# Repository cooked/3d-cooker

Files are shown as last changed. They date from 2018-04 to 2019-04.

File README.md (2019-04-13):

# wreck3D 

The wreck3D is a parametric delta printer built around the OpenBuilds V-Slot 2040 linear rails.   

The wreck3D design is made simple so that the built is achieved, with the same minimal set of 3D printed parts, in virtually any form-factor the OpenBuilds rails allow.

## Size
List of the build sizes readily available:  

* wreck3D-S (Build Volume: 200x185 mm) 
* wreck3D-M (Build Volume: 250x300 mm)

[3D printed parts](printed-parts) - [Bill of Material](bom/bom.csv) - [Manual](https://github.com/wreck-lab/wreck3D/wiki)
   
##
      
Analytics (https://github.com/igrigorik/ga-beacon)

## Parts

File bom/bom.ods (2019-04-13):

Item | Quantity | Note | Source
OpenBuild VSlot 2040 1000mm | 3 | Frame S – cut to 250 + 250 + 500 mm | RatRig (http://www.ratrig.com/hardware2/vslot/v-slot-2040.html))
OpenBuild VSlot 2040 1000mm | 3 | Frame M - cut to 300 + 700 mm | RatRig (http://www.ratrig.com/hardware2/vslot/v-slot-2040.html))
OpenBuild VSlot 2020 1000mm | 2 | Frame M - cut to 300 + 300 +300 mm | RatRig (http://www.ratrig.com/hardware2/vslot/v-slot-2020.html))
carbon fiber tube 8x6x500mm | 3 | Frame S – request cuts of 245 mm each The length of the arms doesn't need to be the exact but SHALL BE THE SAME for all of them. Trim them down with sandpaper if the difference is visible to the naked eye | AliExpress (https://www.aliexpress.com/item/2pcs-3K-Matte-Twill-Carbon-Fiber-Tube-Pipe-OD-8mm-ID-6mm-Length-500mm-Tubes-Twill/32760008446.html)
carbon fiber tube 8x6x1000mm | 2 | Frame M – request cuts of 330 mm each The length of the arms doesn't need to be the exact but SHALL BE THE SAME for all of them. Trim them down with sandpaper if the difference is visible to the naked eye | AliExpress (https://www.aliexpress.com/item/2pcs-3K-Matte-Twill-Carbon-Fiber-Tube-Pipe-OD-8mm-ID-6mm-Length-500mm-Tubes-Twill/32760008446.html)
220x3mm round aluminum heat bed | 1 |  | AliExpress (https://www.aliexpress.com/item/MK3-Heat-bed-220-3mm-Aluminum-Heatbed-dual-power-12V-or-24V-round-PCB-Heat-bed/32810724832.html)
OpenBuild VSlot mini wheel | 9 | 3x each carriage | AliExpress (https://www.aliexpress.com/item/10pcs-Openbuilds-V-Slot-Linear-Extrusion-Wheels-Delrin-plastic-Idler-Pulley-For-guide-rail-3D-Printer/32623054810.html)
NEMA 17 stepper motor | 4 | cable included | AliExpress (https://www.aliexpress.com/item/5pcs-lot-Free-Shipping-3D-printer-4-lead-Nema17-Stepper-Motor-42-motor-Nema-17-motor/32728425552.html)
GT2 Pulley 20 teeth 5mm bore | 3 | lock on motor shaft with set screws | AliExpress (https://www.aliexpress.com/item/POWGE-GT2-Timing-Pulley-20-teeth-Bore-5mm-6mm-6-35mm-8mm-for-Width-6mm-GT2/32226562320.html)
GT2 Pulley 16 teeth 3mm bore | 3 |  | AliExpress (https://www.aliexpress.com/item/New-GT2-Idler-Timing-Pulley-Bearing-20T-3-5mm-Bore-20-Teeth-Suitable-For-6mm-Belt/32823859861.html)
GT2 Timing Belt 6mm width | 6m |  | AliExpress (https://www.aliexpress.com/item/POWGE-GT2-timing-belt-width-6mm-Rubber-2GT-6mm-used-in-linear-drive-Small-Backlash-2GT/2039635559.html)
10mm steel ball M4 thread | 12 | 3x carriages 3x effector | AliExpress (https://www.aliexpress.com/item/High-Quality-Brand-New-16pcs-Set-10mm-M4-Threaded-Steel-Ball-Rod-Ends-For-Kossel-3D/32646492682.html)
6x13mm magnet rod | 12 | 2x each arm | Supermagnete (https://www.supermagnete.de/eng/rod-magnets-neodymium/rod-magnet-diameter-6mm-height-13mm-neodymium-n48-nickel-plated_S-06-13-N)
V6 lite hotend kit |  | or original V6 all-metal hotend | e3d-online (https://e3d-online.com/lite6)
12V 15A power supply | 1 |  | AliExpress (https://www.aliexpress.com/item/2016-Brand-New-Mini-Size-Led-Power-Supply-12V-5A-8-5A-10A-12-5A-15A/32571488140.html)
KW-1-2A micro switch | 1 | remove lever | AliExpress (https://www.aliexpress.com/item/Free-Shipping-100pcs-KW-1-2A-Small-lever-micro-limit-switch/32546855308.html)
KW11-B switch | 3 | remove lever | AliExpress (https://www.aliexpress.com/item/50-pieces-lot-KW11-B-microswitch-3pins-3P-5A-125-250V-10T85-18mm-long-handle/32528115223.html)
40x10mm radial blow fan | 2 | 2x effector print cooling fan | AliExpress (https://www.aliexpress.com/item/2PCS-Gdstime-3D-Printer-Accessories-12V-4010-Turbo-Fan-Blower-Cooling-Fans/32798634077.html)
M5x8mm hex screw low profile | 100 | 12x each motor and idler corner | AliExpress (https://www.aliexpress.com/item/Low-profile-screws-M5-8-100pcs/32660374302.html)
M5 T-nut hammer head | 100 | 12x each motor and idler corner | AliExpress (https://www.aliexpress.com/item/100pcs-lot-High-Quality-T-nut-Hammer-Head-Fasten-Nut-M5-Connector-Nickel-Plated-for-20/32716318190.html)
M4x10mm screw DIN 912 | 12 | 3x carriage 3x effector | AliExpress (https://www.aliexpress.com/item/M4-series-100pcs-Stainless-steel-hex-socket-screws-M4-4-5-6-8-10-12-30/32662311536.html)
M5x20mm screw DIN 912 | 3 | idler pulley mount | AliExpress (https://www.aliexpress.com/item/QINTIDES-M5-Hexagon-socket-head-cap-screws-304-stainless-steel-hexagon-screw-DIN-912-M5/32860098615.html)
M5x16mm screw DIN 912 | 9 | 3x carriage wheels | AliExpress (https://www.aliexpress.com/item/QINTIDES-M5-Hexagon-socket-head-cap-screws-304-stainless-steel-hexagon-screw-DIN-912-M5/32860098615.html)
M3x10mm screw DIN 912 | 12 | 4x each stepper motor mount | AliExpress (https://www.aliexpress.com/item/250pc-set-M3-Cap-Button-Flat-Head-A2-Stainless-Steel-Hex-Socket-Screws-Bolt-With-Hex/32775208136.html)
M3x20mm screw DIN 912 | 1 | 1x effector tower spring | AliExpress (https://www.aliexpress.com/item/250pc-set-M3-Cap-Button-Flat-Head-A2-Stainless-Steel-Hex-Socket-Screws-Bolt-With-Hex/32775208136.html)
M3x30mm screw DIN 912 | 2 | 2x effector tower collar | AliExpress (https://www.aliexpress.com/item/250pc-set-M3-Cap-Button-Flat-Head-A2-Stainless-Steel-Hex-Socket-Screws-Bolt-With-Hex/32775208136.html)
M3x40mm screw DIN 912 | 1 | 1x effector tower rotation | AliExpress (https://www.aliexpress.com/item/250pc-set-M3-Cap-Button-Flat-Head-A2-Stainless-Steel-Hex-Socket-Screws-Bolt-With-Hex/32775208136.html)
M2.5x12mm screw DIN 912 | 6 | 6x endstop switches | AliExpress (https://www.aliexpress.com/item/100pcs-Lot-Metric-Thread-DIN912-M2-5x12-mm-M2-5-12-mm-Black-Grade-12-9/32808680386.html)
M3 nut | 9 | 3x for effector 3x belt lock mounts 3x belt tensioners | AliExpress (https://www.aliexpress.com/item/Free-shipping-100pcs-lot-Metric-thread-DIN934-M3-304-Stainless-Steel-Hex-Nuts/32405600179.html)
M2x8mm screw self tapping | 4 | 2x (each) effector print cooling fan | AliExpress (https://www.aliexpress.com/item/100pcs-Lot-Metric-Thread-carbon-steel-Hex-Socket-Head-Cap-self-tapping-Screw-Bolts-M2x8/32497369062.html)
3mm grommet | 1 | 1x effector tower spring | AliExpress (https://www.aliexpress.com/item/130pcs-3mm-Inner-Dia-Double-Sides-Wire-Grommets-Gasket-Cable-Protector/32824763799.html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)

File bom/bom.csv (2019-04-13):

Item | Quantity | Note | Source
OpenBuild VSlot 2040 1000mm | 3 | Frame S - cut to 250 + 250 + 500 mm | RatRig
OpenBuild VSlot 2040 1000mm | 3 | Frame M - cut to 300 + 700 mm | RatRig
OpenBuild VSlot 2020 1000mm | 2 | Frame M - cut to 300 + 300 +300 mm | RatRig
carbon fiber tube 8x6x500mm | 3 | Frame S – request cuts of 245 mm each The length of the arms doesn't need to be the exact but SHALL BE THE SAME for all of them. Trim them down with sandpaper if the difference is visible to the naked eye | AliExpress
carbon fiber tube 8x6x1000mm | 2 | Frame M – request cuts of 330 mm each The length of the arms doesn't need to be the exact but SHALL BE THE SAME for all of them. Trim them down with sandpaper if the difference is visible to the naked eye | AliExpress
220x3mm round aluminum heat bed | 1 |  | AliExpress
OpenBuild VSlot mini wheel | 9 | 3x each carriage | AliExpress
NEMA 17 stepper motor | 4 | cable included | AliExpress
GT2 Pulley 20 teeth 5mm bore | 3 | lock on motor shaft with set screws | AliExpress
GT2 Pulley 16 teeth 3mm bore | 3 |  | AliExpress
GT2 Timing Belt 6mm width | 6m |  | AliExpress
10mm steel ball M4 thread | 12 | 3x carriages 3x effector | AliExpress
6x13mm magnet rod | 12 | 2x each arm | Supermagnete
V6 lite hotend kit |  | or original V6 all-metal hotend | e3d-online
12V 15A power supply | 1 |  | AliExpress
KW-1-2A micro switch | 1 | remove lever | AliExpress
KW11-B switch | 3 | remove lever | AliExpress
40x10mm radial blow fan | 2 | 2x effector print cooling fan | AliExpress
M5x8mm hex screw low profile | 100 | 12x each motor and idler corner | AliExpress
M5 T-nut hammer head | 100 | 12x each motor and idler corner | AliExpress
M4x10mm screw DIN 912 | 12 | 3x carriage 3x effector | AliExpress
M5x20mm screw DIN 912 | 3 | idler pulley mount | AliExpress
M5x16mm screw DIN 912 | 9 | 3x carriage wheels | AliExpress
M3x10mm screw DIN 912 | 12 | 4x each stepper motor mount | AliExpress
M3x20mm screw DIN 912 | 1 | 1x effector tower spring | AliExpress
M3x30mm screw DIN 912 | 2 | 2x effector tower collar | AliExpress
M3x40mm screw DIN 912 | 1 | 1x effector tower rotation | AliExpress
M2.5x12mm screw DIN 912 | 6 | 6x endstop switches | AliExpress
M3 nut | 9 | 3x for effector 3x belt lock mounts 3x belt tensioners | AliExpress
M2x8mm screw self tapping | 4 | 2x (each) effector print cooling fan | AliExpress
3mm grommet | 1 | 1x effector tower spring | AliExpress

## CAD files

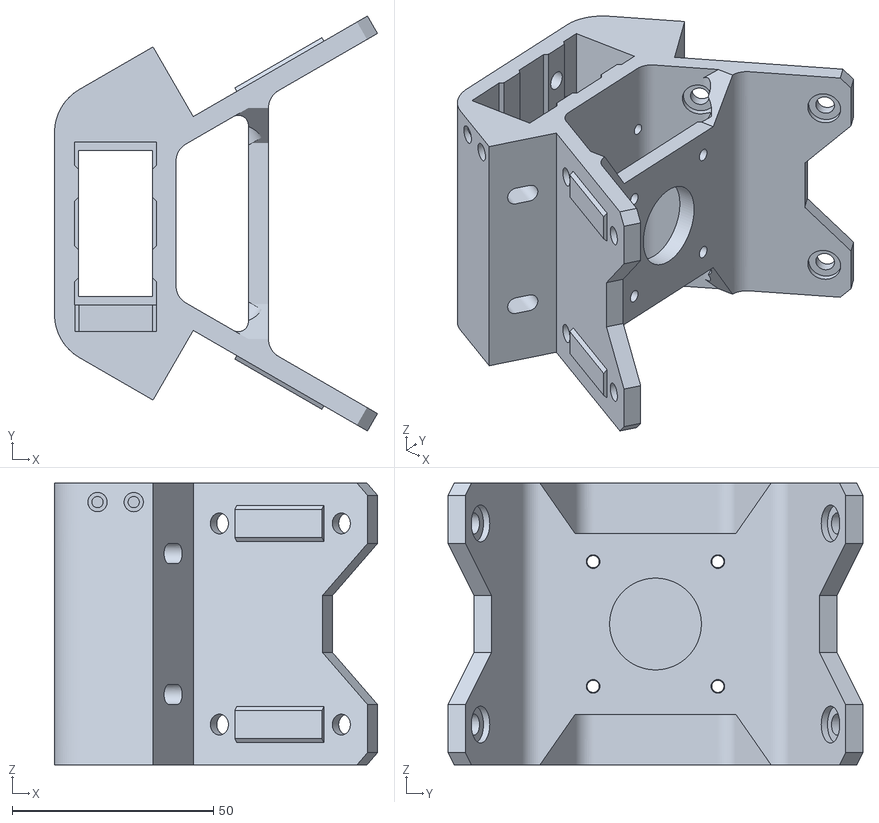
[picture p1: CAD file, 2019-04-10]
printed-parts/corner_motor_2.stl
80.3 x 103.2 x 70.0

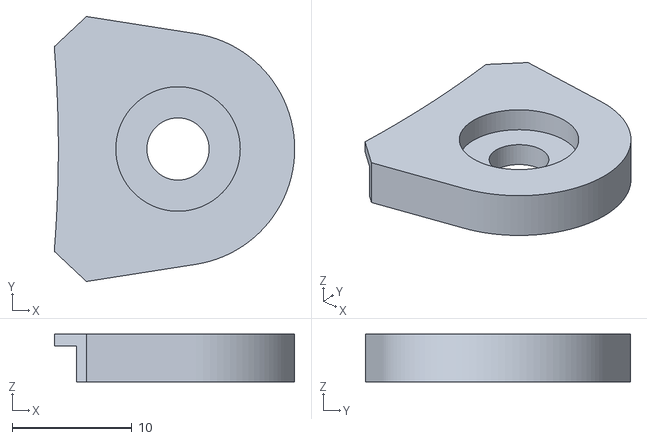
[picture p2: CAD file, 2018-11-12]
printed-parts/misc/bed_clamp_220x3mm.stl
20.1 x 22.1 x 4.00

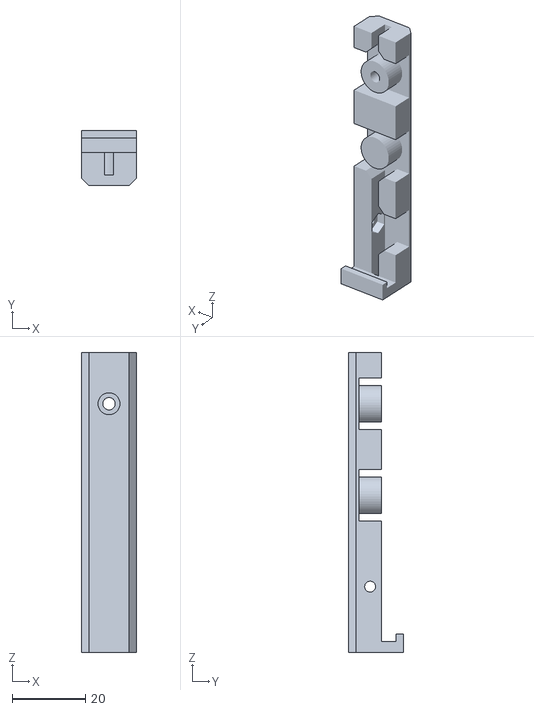
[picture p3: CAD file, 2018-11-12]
printed-parts/carriage_lock.stl
15.0 x 15.0 x 82.0

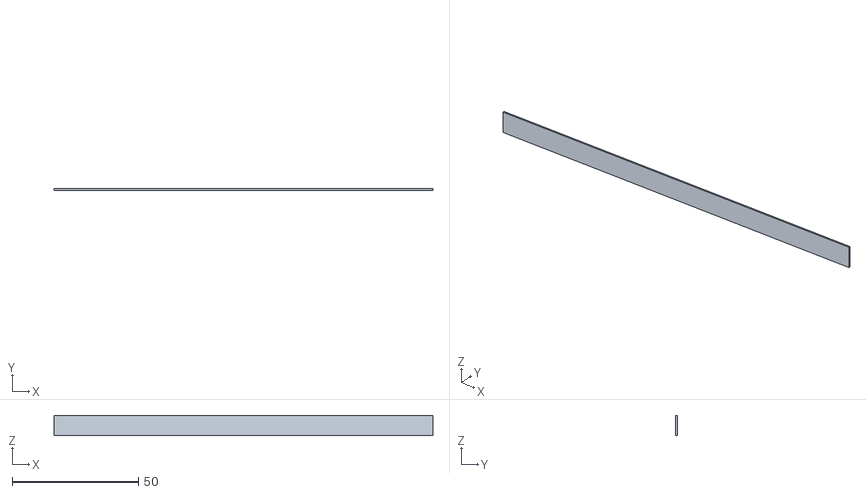
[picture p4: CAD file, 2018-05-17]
printed-parts/misc/rail_cover.stl
150.0 x 0.6 x 8.00

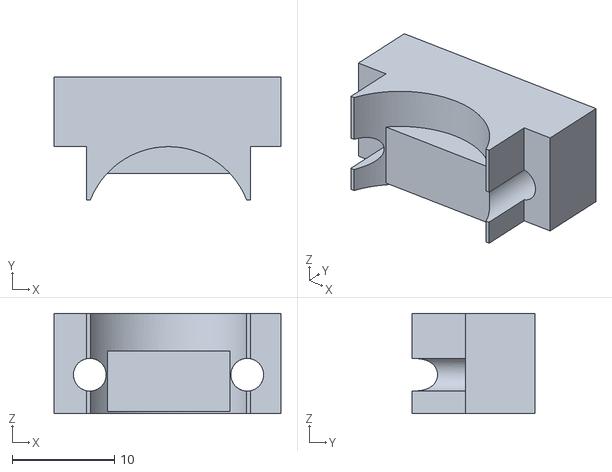
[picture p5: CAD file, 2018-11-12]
printed-parts/effector_collar.stl
22.2 x 12.0 x 9.80

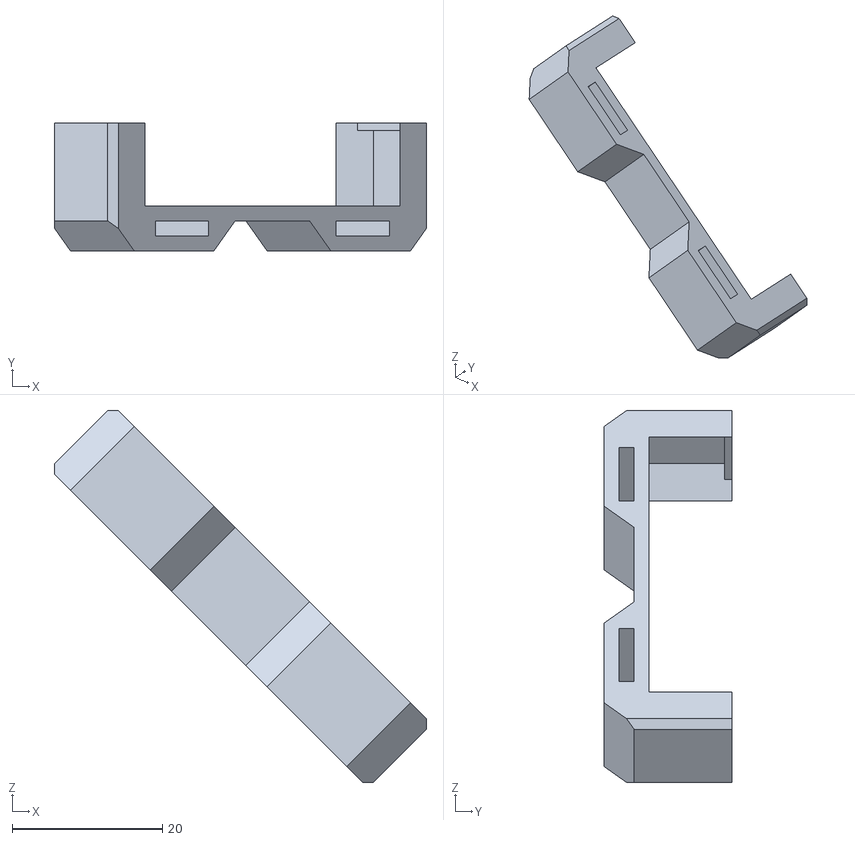
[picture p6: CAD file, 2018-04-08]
printed-parts/misc/motor_cable_organizer.stl
49.5 x 17.0 x 49.5

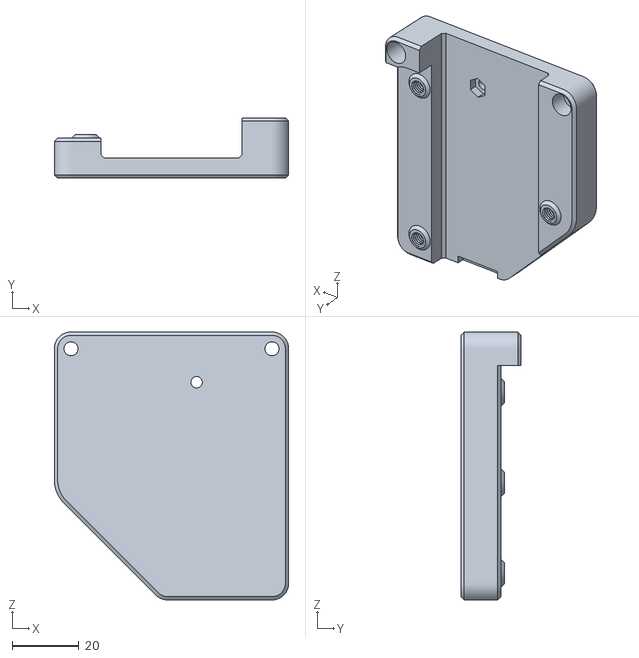
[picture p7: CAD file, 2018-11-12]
printed-parts/carriage_body.stl
70.0 x 18.0 x 80.0

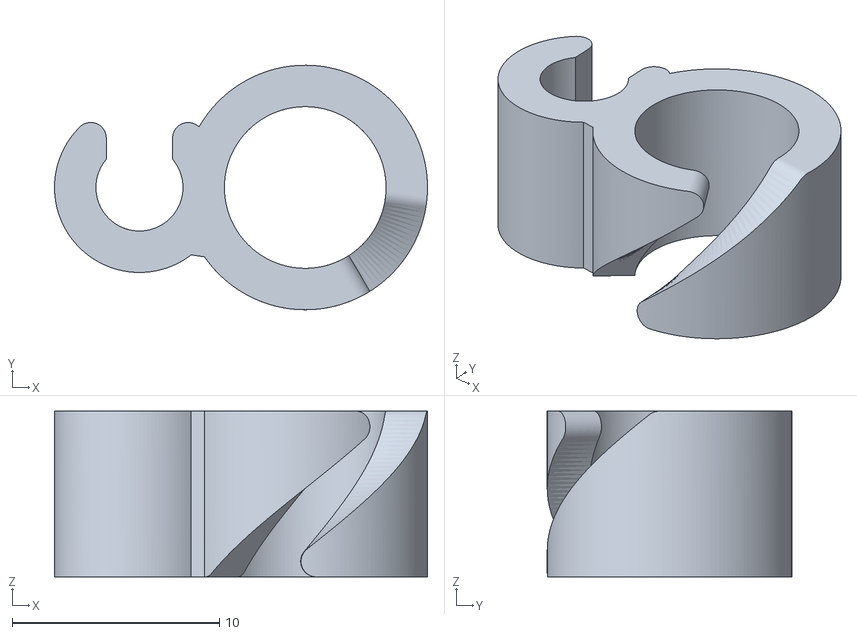
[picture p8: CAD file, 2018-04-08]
printed-parts/misc/cable_clip.stl
18.0 x 11.8 x 8.00

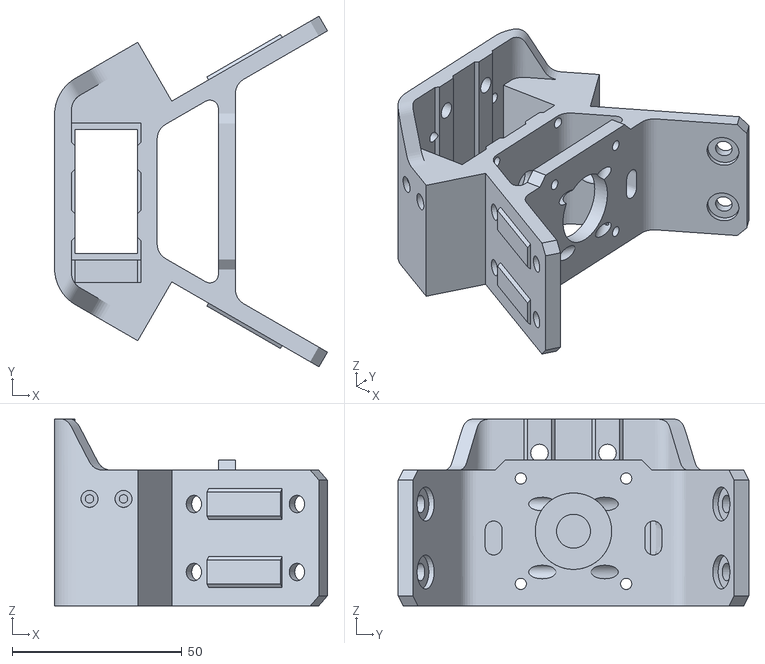
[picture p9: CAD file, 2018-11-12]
printed-parts/corner_motor.stl
80.3 x 103.2 x 55.0

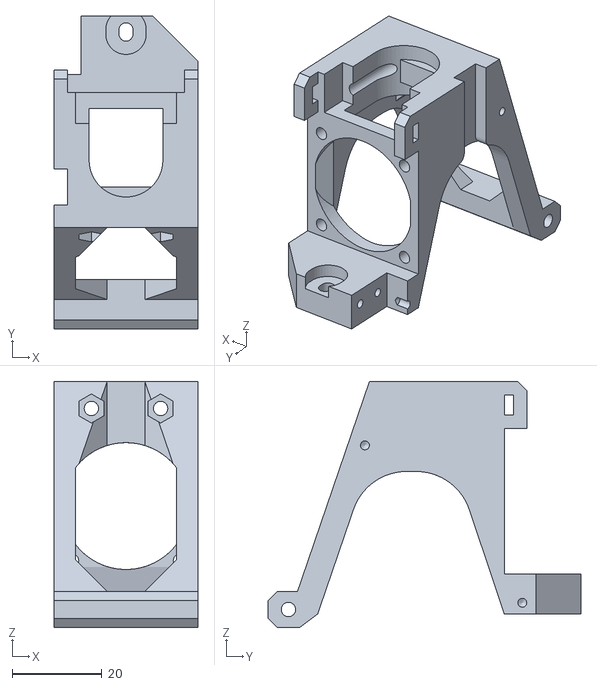
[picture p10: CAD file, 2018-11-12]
printed-parts/effector_tower.stl
32.0 x 69.5 x 54.7

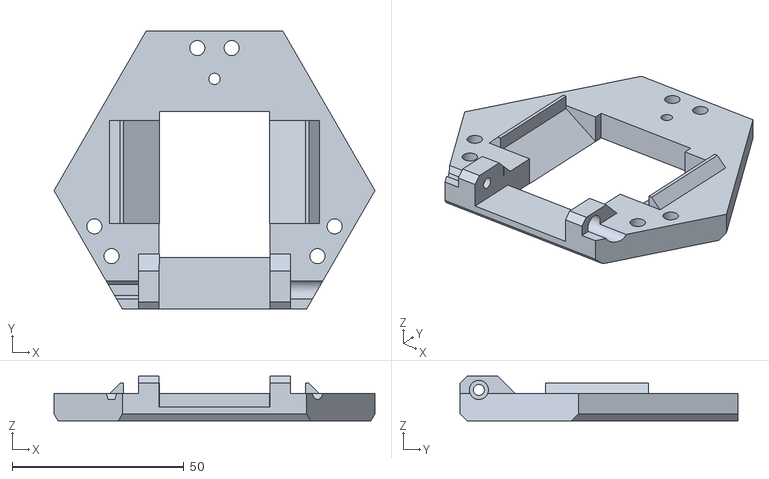
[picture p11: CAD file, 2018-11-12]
printed-parts/effector_base.stl
93.5 x 81.0 x 13.0

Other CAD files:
printed-parts/corner_idler.stl

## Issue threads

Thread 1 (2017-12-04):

M4 holes in the carriage are too small.

orlandod543, 2017-12-04:
The M4 screws to hold the steel balls have a round head with a diameter of 6.78mm. The hole in the carriage where they fit,  however is 6.58mm. Enhancing it to 7mm should fix the problem.

cooked, 2018-05-10:
- carriage updated to the new version (with the cut corner)
- M4 screw holes diameter is now 7.2 mm

Closed 2018-05-10.

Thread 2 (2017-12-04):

M3 screws and nuts are missing.

orlandod543, 2017-12-04:

cooked, 2018-05-10:
- added set of M3 screws to the BOM

Closed 2018-05-10.

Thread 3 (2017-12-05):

M5 screws for the bearings are missing.

orlandod543, 2017-12-05:
They should be 9 screws of 16mm long.

cooked, 2018-05-10:
- added M5x16 screws to the BOM

Closed 2018-05-10.

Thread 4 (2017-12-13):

Use 10mm m3 screws for the stepper motor

orlandod543, 2017-12-13:
10mm m3 screws are perfect to hold the stepper motors. Longer than that won't work

cooked, 2018-05-10:
- added set of M3 screws to the BOM
- added assembly instruction in the wiki

Closed 2018-05-10.

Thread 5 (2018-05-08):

Replace M5 nut of the idler mount with printed thread

cooked, 2018-05-08:

cooked, 2018-05-13:
updated STL

Closed 2018-05-13.

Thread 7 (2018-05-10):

Merge the BOMs

cooked, 2018-05-10:
- merge the BOM of the different printer sizes to make it easier to maintain
- use the column "notes" to add details on how parts are customized for the specific size

cooked, 2018-05-13:
single BOM created

Closed 2018-05-13.

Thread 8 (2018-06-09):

spheres distance in the effector plate is wrong

cooked, 2018-06-09:
adjacent sphere centers should be 60mm on the long side and 10mm on the short side.
on the long side the distance is currently 59.952

cooked, 2018-11-12:
the sphere holes have been moved to the correct distance of  60mm
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

Closed 2018-11-12.

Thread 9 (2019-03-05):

Print Area

sennalb, 2019-03-05:
Hi,
where I can find print area dimensions ?
Thanks

smark-, 2019-03-06:
> Hi,
> where I can find print area dimensions ?
> Thanks

The wreck3D-S has a build volume of 200x185 mm. I will add them to the Wiki

sennalb, 2019-03-07:
Since wrek3d-s is a parametric printer  is It possible to establish a printing area and obtain the respective dimensions of the towers, sides and rods.
 I have not yet found a calculation system at this level.
Obviously within certain limits, for example if I wanted to get a 250x300 printing area which could be the lengths of the towers, sides and rods?

smark-, 2019-03-08:
Given your volume requirements I would start from the wreck3D-M which has a build volume of 260x275. If you just increase the column height by 25 mm you can easily reach a total height of 300mm. We are planning to release the design files and the mounting instructions in mid April, as we did we the wreck3D-S. If you are need it sooner please send us an e-mail at info@wrecklab.com

Closed 2019-04-15.

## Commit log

2018-04-08 add STL
    [cable_clip.stl, carriage_belt_lock.stl, carriage_body.stl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]
2018-04-08 add settings Cura
    [3DC+mk3.global.cfg]
2018-04-08 add settings Marlin firmware
    [Configuration.h, Configuration_adv.h]
2018-05-08 added animation idler assembly
2018-05-10 updated effector to mk3
    [effector_base.stl, effector_fan_nozzle.stl, effector_lid.stl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]
2018-05-10 add motor mount picture
2018-05-10 add idler mount picture
2018-05-10 added motor base picture
2018-05-10 added base idler picture
2018-05-10 updated carriage
    [carriage_belt_lock.stl, carriage_body.stl]
2018-05-13 replaced nut with M5 threaded hole
    [frame_corner_idler.stl]
2018-05-17 added cable cover for the rails
    [rail_cover.stl]
2018-11-12 updated printed part for release
    [bed_clamp_220x3mm.stl, cable_clip.stl, carriage_belt_lock.stl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]
2018-11-12 removed settings and resources
    [3DC+mk3.global.cfg, Configuration.h, Configuration_adv.h]
2018-12-16 BOM in csv
    [bom.csv]
2019-04-10 added motor corner for frame M
    [corner_motor_2.stl]
2019-04-13 update BOM with frame M
    [bom.csv, bom.ods]
2019-04-13 minor fix in BOM
    [bom.ods]
